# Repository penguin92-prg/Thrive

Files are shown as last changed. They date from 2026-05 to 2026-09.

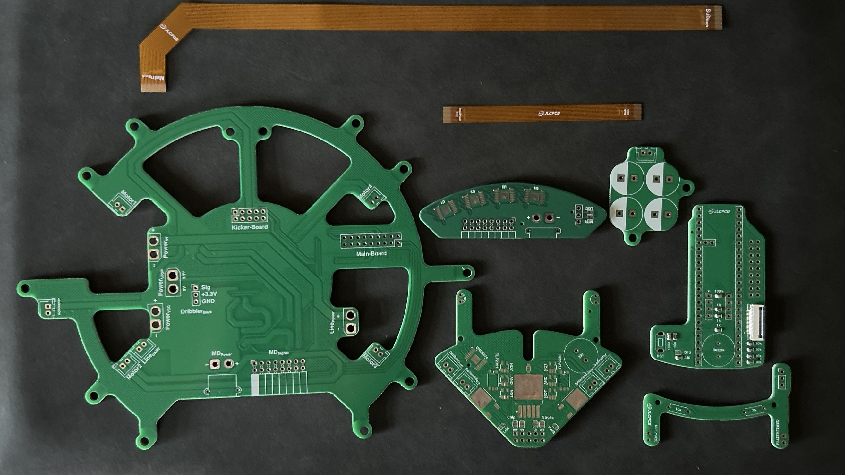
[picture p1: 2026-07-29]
Document/picture_substrate/Order-260707-1.jpg

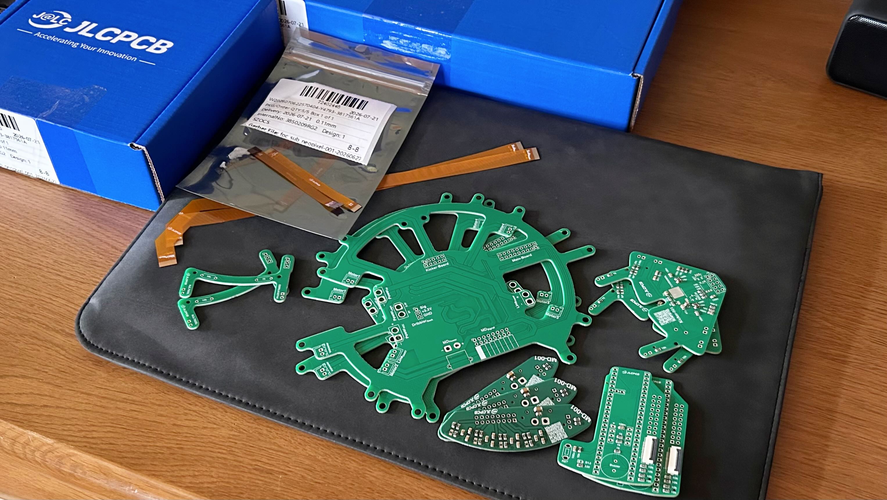
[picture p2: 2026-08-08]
Document/picture_substrate/Order-260707-2.jpg

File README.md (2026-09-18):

# Thrive 2026 Main-repo

このリポジトリは RCJ サッカー オープンリーグ に出場する、チーム Thrive のリポジトリです。

### Follow us!
様々な情報を公開していこうと考えています！ぜひのぞいてみてください！
- X (Twitter) | [@RCJ_thrive](https://x.com/RCJ_thrive)
- YouTube | [@RCJ_thrive](https://youtube.com/@rcj_thrive)
- Team Web Page | [Thrive Blog](https://note.com/rcj_thrive)

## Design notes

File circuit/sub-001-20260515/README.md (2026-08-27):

# サブ基板 001

サブ基板 ver.001のREADME

## 設計者
- @penguin92-prg
- @ryo-robot14

## ピンアサイン

## 使用上の注意

## 使用部品

|No.|Ref.|Name|QTY|Assembled By|Note|URL|
|---|---|---|---|---|---|---|
|001|U1,3,6,8,10|Grove|5|OWN|UnitV用（配線を介すること）|[秋月電子](https://akizukidenshi.com/catalog/g/g131074/)|
|002|U16,17|ESP32C3|2|OWN||[秋月電子](https://akizukidenshi.com/catalog/g/g117454/)<br>[秋月電子](https://akizukidenshi.com/catalog/g/g105779/)|
|003|D1,2,5~10|OSI5FU3A11C|8|OWN|IR-LED|[秋月電子](https://akizukidenshi.com/catalog/g/g104313/)|
|004|R5,6,17,18,27,28,39,40|Resister 47Ω|8|JLCPCB|IRLED用|[JLCPCB](https://jlcpcb.com/partdetail/18402-0805W8F470JT5E/C17714)|
|005|U4,5,12,13,18,19,22,23|NE555DR|8|JLCPCB|タイマーIC|[JLCPCB](https://jlcpcb.com/partdetail/TexasInstruments-NE555DR/C7593)|
|006|C2,3,8,9,14,15,21,22,27,28,33,34,37,38,43,44|Capacitor 10nF|16|JLCPCB|タイマーIC用|[JLCPCB](https://jlcpcb.com/partdetail/2062-CL21B103KBANNNC/C1710)|
|007|C4,5,17,18,29,30,39,40|Capacitor 1nF|8|JLCPCB|タイマーIC用|[JLCPCB](https://jlcpcb.com/partdetail/47657-CL21B102KBCNNNC/C46653)|
|008|C10,11,24,25,35,36,45,46|Capacitor 10uF|8|JLCPCB|タイマーIC用|[JLCPCB](https://jlcpcb.com/partdetail/439567-GRM21BR61H106KE43L/C440198)|
|009|R1,2,11,12,23,24,33,34|Resister 18kΩ|8|JLCPCB|タイマーIC用|[JLCPCB](https://jlcpcb.com/partdetail/18194-0805W8F1802T5E/C17506)|
|010|R3,4,13,14,25,26,37,38|Resister 1.5kΩ|8|JLCPCB|タイマーIC用|[JLCPCB](https://jlcpcb.com/partdetail/4717-0805W8F1501T5E/C4310)|
|011|R7,8,19,20,29,30,41,42|Resister 100Ω|8|JLCPCB|タイマーIC用|[JLCPCB](https://jlcpcb.com/partdetail/18096-0805W8F1000T5E/C17408)|
|012|R9,10,21,22,31,32,43,44|Resister 1kΩ|8|JLCPCB|タイマーIC用|[JLCPCB](https://jlcpcb.com/partdetail/18201-0805W8F1001T5E/C17513)|
|013|Q1~8|BSS138|8|OWN|NchMOSFET|[秋月電子](https://akizukidenshi.com/catalog/g/g104232/)|
|014|U20,21,24,25|tssp58038|4|OWN|IR Sensor|[秋月電子](https://akizukidenshi.com/catalog/g/g129594/)|
|015|C41/C42/C47/C48|Capacitor 0.33uF|4|JLCPCB|tssp58038用|[JLCPCB](https://jlcpcb.com/partdetail/2092-0805B334K500NT/C1740)|
|016|R35/R36/R45/R46|Resister 39kΩ|4|JLCPCB|tssp58038用|[JLCPCB](https://jlcpcb.com/partdetail/26569-0805W8F3902T5E/C25826)|
|017|U2,7,9,11,14,15|LM1117GS-3.3|6|OWN|3.3V生成3端子レギュレータ|[秋月電子](https://akizukidenshi.com/catalog/g/g116989/)|
|018|C1,6,7,12,13,16,19,20,23,26,31,32|Capacitor 10uF|12|JLCPCB|3端子レギュレータ用|[JLCPCB](https://jlcpcb.com/partdetail/439567-GRM21BR61H106KE43L/C440198)|
|019|D3|OSR50603C1E|1|OWN|5V給電確認用赤色LED|[秋月電子](https://akizukidenshi.com/catalog/g/g108274/)|
|020|D4|OSG50603C1E|1|ONW|3.3V給電確認用緑色LED|[秋月電子](https://akizukidenshi.com/catalog/g/g108275/)|
|021|R15,16|Resister 330Ω|2|JLCPCB|LED用抵抗器|[JLCPCB](https://jlcpcb.com/partdetail/18318-0805W8F3300T5E/C17630)|
|022|U26~29|HC-SR04|4|OWN|USS|[秋月電子](https://akizukidenshi.com/catalog/g/g111009/)|
|023|R47,48|Resister 10kΩ|2|JLCPCB|トグルスイッチプルアップ用抵抗器|[JLCPCB](https://jlcpcb.com/partdetail/18102-0805W8F1002T5E/C17414)|
|024|J1|AFC01_S12FCA00|1|JLCPCB|ネオピクセル基板へのFPCコネクタ|[JLCPCB](https://jlcpcb.com/partdetail/JUSHUO-AFC01_S12FCA00/C262661)|
|025|J2|ピンソケット 01x02|1|OWN|電源基板へのピンソケット|[秋月電子](https://akizukidenshi.com/catalog/g/g105779/)|
|026|J3|XT30U-M|1|OWN|電源基板へのXT30コネクタ|[秋月電子](https://akizukidenshi.com/catalog/g/g117951/)|
|027|J4|AFC01_S18FCA00|1|JLCPCB|メイン基板へのFPCコネクタ|[JLCPCB](https://jlcpcb.com/partdetail/JUSHUO-AFC01_S18FCA00/C262666)|

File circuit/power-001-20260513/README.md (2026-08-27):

# [基板名] [バージョン番号]

[基板名] ver.[バージョン番号]のREADME

## 設計者
- @penguin92-prg
- @ryo-robot14

## ピンアサイン

## 使用上の注意

## 使用部品

|No.|Ref.|Name|QTY|Assembled By|Note|URL|
|---|---|---|---|---|---|---|
|001|J1|Vin|1|OWN|not connected|--|
|002|J2,3,4,5|+5V_Line / Power / Logic / Sub_Power|4|OWN|XT30PW-M|[秋月電子](https://akizukidenshi.com/catalog/g/g117949/)|
|001|J6|Sub_Signal|1|OWN|ピンヘッダ 01x02|[秋月電子](https://akizukidenshi.com/catalog/g/g112986/)|
|001|J8|ESC|1|OWN|not connected|--|
|002|F1|Fuse 10A|1|OWN|ヒューズホルダー・ヒューズ|[秋月電子](https://akizukidenshi.com/catalog/g/g110521/)<br>[秋月電子](https://akizukidenshi.com/catalog/g/g107132/)|
|003|SW4|DS-850K-S-ON-K|1|OWN|ロッカースイッチ|[秋月電子](https://akizukidenshi.com/catalog/g/g115740/)|
|004|U5|PIC12F683T-I/SN|1|OWN|電圧監視IC|[秋月電子](https://akizukidenshi.com/catalog/g/g102034/)|
|005|C12|Capacitor 100nF|1|JLCPCB|電圧監視IC用コンデンサ|[JLCPCB](https://jlcpcb.com/partdetail/YAGEO-CC0805KRX7R9BB104/C49678)|
|006|R14|Resister 30kΩ|1|JLCPCB|電圧監視IC用抵抗器|[JLCPCB](https://jlcpcb.com/partdetail/18309-0805W8F3002T5E/C17621)|
|007|R15|Resister 10kΩ|2|JLCPCB|電圧監視IC用抵抗器|[JLCPCB](https://jlcpcb.com/partdetail/18102-0805W8F1002T5E/C17414)
|008|U6|LM1117GS-3.3|1|OWN|電圧監視IC用3端子レギュレータ|[秋月電子](https://akizukidenshi.com/catalog/g/g116989/)|
|009|C5,13|Capacitor 10uF|2|JLCPCB|3端子レギュレータ用コンデンサ|[JLCPCB](https://jlcpcb.com/partdetail/439567-GRM21BR61H106KE43L/C440198)|
|010|Q1|BSS138|1|OWN|NchMOSFET|[秋月電子](https://akizukidenshi.com/catalog/g/g104232)|
|011|Q2|TJ60S04M3L|1|OWN|PchパワーMOSFET|[秋月電子](https://akizukidenshi.com/catalog/g/g116297/)|
|012|R18|Resister 100Ω|1|JLCPCB||[JLCPCB](https://jlcpcb.com/partdetail/18096-0805W8F1000T5E/C17408)|
|013|R19,20|Resister 10kΩ|2|JLCPCB||[JLCPCB](https://jlcpcb.com/partdetail/18102-0805W8F1002T5E/C17414)|
|014|BZ1|PKM13EPYH4000-A0|1|OWN|電圧監視用ブザー|[秋月電子](https://akizukidenshi.com/catalog/g/g104118/)|
|015|R17|Resister 1.2kΩ|1|JLCPCB|ブザー用抵抗器|[JLCPCB](https://jlcpcb.com/partdetail/18067-0805W8F1201T5E/C17379)|
|016|C1|Capacitor 470uF|1|OWN||[秋月電子](https://akizukidenshi.com/catalog/g/g117883/)|
|017|U1,2|OKL-T/6-W12N-C|2|OWN|DCDC|[秋月電子](https://akizukidenshi.com/catalog/g/g106187/)|
|018|R4,5|Resister 20kΩ|2|JLCPCB|DCDC用抵抗器|[JLCPCB](https://jlcpcb.com/partdetail/4735-0805W8F2002T5E/C4328)|
|019|R6,7|Resister 10Ω|2|JLCPCB|DCDC用抵抗器|[JLCPCB](https://jlcpcb.com/partdetail/18103-0805W8F100JT5E/C17415)|
|020|R8,R10|Resister 1kΩ|2|JLCPCB|DCDC用抵抗器|[JLCPCB](https://jlcpcb.com/partdetail/18201-0805W8F1001T5E/C17513)|
|020|R9,11|Resister 330Ω|2|JLCPCB|DCDC用抵抗器|[JLCPCB](https://jlcpcb.com/partdetail/18318-0805W8F3300T5E/C17630)|
|020|R12,13|Resister 1.2kΩ|2|JLCPCB|DCDC用抵抗器|[JLCPCB](https://jlcpcb.com/partdetail/18067-0805W8F1201T5E/C17379)|
|020|C6,7|Capacitor 22uF|2|JLCPCB|DCDC用コンデンサ|[JLCPCB](https://jlcpcb.com/partdetail/46786-CL21A226MAQNNNE/C45783)|
|020|C10,11|Capacitor 10uF|2|JLCPCB|DCDC用コンデンサ|[JLCPCB](https://jlcpcb.com/partdetail/439567-GRM21BR61H106KE43L/C440198)|
|020|U3|AZ1084C-3.3|1|OWN|3端子レギュレータ|[秋月電子](https://akizukidenshi.com/catalog/g/g117598/)|
|020|C8|Capacitor 10uF|1|JLCPCB|3端子レギュレータ用コンデンサ|[JLCPCB](https://jlcpcb.com/partdetail/439567-GRM21BR61H106KE43L/C440198)|
|020|C9|Capacitor 22uF|1|JLCPCB|3端子レギュレータ用コンデンサ|[JLCPCB](https://jlcpcb.com/partdetail/46786-CL21A226MAQNNNE/C45783)|
|020|SW1,2|トグルスイッチ|1|OWN||[秋月電子](https://akizukidenshi.com/catalog/g/g102399/)|
|020|C2,3|Capacitor 100nF|2|JLCPCB|トグルスイッチ用コンデンサ|[JLCPCB](https://jlcpcb.com/partdetail/YAGEO-CC0805KRX7R9BB104/C49678)|

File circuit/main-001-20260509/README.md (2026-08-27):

# Main 001

メイン基板 ver.001のREADME

## 設計者
- @ryo-robot14
- @penguin92-prg

## ピンアサイン

## 使用上の注意

## 使用部品

|No.|Ref.|Name|QTY|Assembled By|Note|URL|
|---|---|---|---|---|---|---|
|001|U1|Teensy4.1|1|OWN|側面の24ピン×2に加えてSDスロット側の5ピンのうち2ピンもつける必要アリ|[PJRC](https://www.pjrc.com/store/teensy41.html)<br>[秋月電子](https://akizukidenshi.com/catalog/g/g105779/)|
|002|U2|BNO055 Module|1|OWN||[秋月電子](https://akizukidenshi.com/catalog/g/g116996/)|
|003|J1|ピンヘッダ 02x09|1|OWN|基板カッターで02x09に加工する必要がある|[秋月電子](https://akizukidenshi.com/catalog/g/g100082/)|
|004|Q1/Q2|BSS138|2|OWN|UART通信のレベル変換用|[秋月電子](https://akizukidenshi.com/catalog/g/g104232)|
|005|J2|AFC01-S18FCA-00|1|JLCPCB|サブ基板へのFPCコネクタ|[JLCPCB](https://jlcpcb.com/partdetail/JUSHUO-AFC01_S18FCA00/C262666)|
|006|BZ1|PKM13EPYH4000-A0|1|OWN|ブザー|[秋月電子](https://akizukidenshi.com/catalog/g/g104118/)|
|007|SW1|TVBP06-B043CW-B|1|OWN|白タクトスイッチ|[秋月電子](https://akizukidenshi.com/catalog/g/g108074/)|
|008|D1|OSWT1608C1A|1|OWN|青色LED(SMD)|[秋月電子](https://akizukidenshi.com/catalog/g/g103986/)|

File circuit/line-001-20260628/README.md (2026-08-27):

# ラインセンサ基板 001

ラインセンサ基板 ver.001のREADME

## 設計者
- @penguin92-prg
- @ryo-robot14

## ピンアサイン

## 使用上の注意

## 使用部品

|No.|Ref.|Name|QTY|Assembled By|Note|URL|
|---|---|---|---|---|---|---|
|001|D1~40|OSR5JA3Z74A|40|OWN|赤色LED|[秋月電子](https://akizukidenshi.com/catalog/g/g111577/)|
|002|R41~72,77~80|Resister 10kΩ|34|JLCPCB|LED用75Ω|[JLCPCB](https://jlcpcb.com/partdetail/21350-0805W8F750JT5E_SMTonly/C20638)|
|003|Q1~40|NJL7502L|40|OWN|フォトトランジスタ|[秋月電子](https://akizukidenshi.com/catalog/g/g102325/)|
|004|R1~32,38,40|Resister 10kΩ|34|JLCPCB|プルダウン用100kΩ|[JLCPCB](https://jlcpcb.com/partdetail/18102-0805W8F1002T5E/C17414)|
|005|U1~16,19,20|LM339DR|20|JLCPCB|コンパレータ|[JLCPCB](https://jlcpcb.com/partdetail/TexasInstruments-LM393DR/C67470)|
|006|C1~16,23,24|Capacitor 100nF|20|JLCPCB|コンパレータ用バイパスコンデンサ|[JLCPCB](https://jlcpcb.com/partdetail/YAGEO-CC0805KRX7R9BB104/C49678)|
|007|C21,22,26,27|Capacitor 10uF|4|JLCPCB|PWM平滑化用コンデンサ|[JLCPCB](https://jlcpcb.com/partdetail/439567-GRM21BR61H106KE43L/C440198)|
|008|R83,84,87,88|Resister 1kΩ|4|JLCPCB|PWM平滑化用抵抗器|[JLCPCB](https://jlcpcb.com/partdetail/18201-0805W8F1001T5E/C17513)|
|009|U17|ATMega2560-16A|1|OWN||[秋月電子](https://akizukidenshi.com/catalog/g/g116567/)|
|010|C28|Capacitor 100nF|1|JLCPCB|ATMegaARFF用コンデンサ|[JLCPCB](https://jlcpcb.com/partdetail/YAGEO-CC0805KRX7R9BB104/C49678)|
|011|SW1|TVBP06-B043C|1|OWN|ATMegaRST用白色タクトスイッチ|[秋月電子](https://akizukidenshi.com/catalog/g/g108074/)|
|012|C18|Capacitor 100nF|1|JLCPCB|ATMegaRST用コンデンサ|[JLCPCB](https://jlcpcb.com/partdetail/YAGEO-CC0805KRX7R9BB104/C49678)|
|013|R81|Resister 10kΩ|1|JLCPCB|ATMegaRST用抵抗器|[JLCPCB](https://jlcpcb.com/partdetail/18102-0805W8F1002T5E/C17414)|
|014|C20|Capacitor 100uF|1|JLCPCB|ATMega用バルクコンデンサ|[JLCPCB](https://jlcpcb.com/partdetail/15681-CL31A107MQHNNNE/C15008)|
|015|C34~38|Capacitor 100nF|5|JLCPCB|ATMega用バイパスコンデンサ|[JLCPCB](https://jlcpcb.com/partdetail/YAGEO-CC0805KRX7R9BB104/C49678)|
|016|SW2|SS12D01G4|1|OWN|5V切り替え用スライドスイッチ|[秋月電子](https://akizukidenshi.com/catalog/g/g112723/)|
|017|J3|コネクタハウジング 02x03|1|OWN|ICSP用ハウジング（配線を介すること）|[秋月電子](https://akizukidenshi.com/catalog/g/g112435/)|
|018|D41|OSG50603C1E|1|OWN|信号緑色LED|[秋月電子](https://akizukidenshi.com/catalog/g/g108275/)|
|019|D42|OSWT1608C1A|1|OWN|信号青色LED|[秋月電子](https://akizukidenshi.com/catalog/g/g103986/)|
|020|R85,86|Resister 330Ω|2|JLCPCB|LED用抵抗器|[JLCPCB](https://jlcpcb.com/partdetail/18318-0805W8F3300T5E/C17630)|
|021|U18|CH340G|1|OWN|USB-UART変換IC|[秋月電子](https://akizukidenshi.com/catalog/g/g113544/)|
|022|C31,32,33|Capacitor 100nF|3|JLCPCB|CH340G用コンデンサ|[JLCPCB](https://jlcpcb.com/partdetail/YAGEO-CC0805KRX7R9BB104/C49678)|
|023|R93|Resister 4.7kΩ|1|JLCPCB|CH340G用抵抗器|[JLCPCB](https://jlcpcb.com/partdetail/18361-0805W8F4701T5E/C17673)|
|024|Y1|Crystal 16MHz|1|OWN|クリスタル|[秋月電子](https://akizukidenshi.com/catalog/g/g108671/)|
|025|C17,19|Capacitor 22pF|2|JLCPCB|クリスタル用コンデンサ|[JLCPCB](https://jlcpcb.com/partdetail/2005-CL10C220JB8NNNC/C1653)|
|026|R82|Resister 1MΩ||JLCPCB|クリスタル用抵抗器|[JLCPCB](https://jlcpcb.com/partdetail/18202-0805W8F1004T5E/C17514)|
|027|Y2|Crystal 12MHz|1|OWN|クリスタル|[秋月電子](https://akizukidenshi.com/catalog/g/g108669/)|
|028|C29,30|Capacitor 22pF|2|JLCPCB|クリスタル用コンデンサ|[JLCPCB](https://jlcpcb.com/partdetail/2005-CL10C220JB8NNNC/C1653)|
|029|R89|Resister 1MΩ|1|JLCPCB|クリスタル用抵抗器|[JLCPCB](https://jlcpcb.com/partdetail/18202-0805W8F1004T5E/C17514)|
|030|P1|USB Type-C|1|OWN|1|[秋月電子](https://akizukidenshi.com/catalog/g/g114356/)|
|031|R90,91|Resister 5.1kΩ|2|JLCPCB|USB用抵抗器|[JLCPCB](https://jlcpcb.com/partdetail/28584-0805W8F5101T5E/C27834)|
|032|D43|CH213K|1|OWN|USB用理想ダイオード|[秋月電子](https://akizukidenshi.com/catalog/g/g129462/)|
|033|D44|OSR50603C1E|1|OWN|VBUS確認用LED|[秋月電子](https://akizukidenshi.com/catalog/g/g108274/)|
|034|R92|Resister 330Ω|1|JLCPCB|VBUS確認用抵抗器|[JLCPCB](https://jlcpcb.com/partdetail/18318-0805W8F3300T5E/C17630)|
|035|J1|XT30U-M|1|OWN|供給基板との接続|[秋月電子](https://akizukidenshi.com/catalog/g/g117951/)|
|036|J2|---|-|---|2pin配線を直接実装すること|---|

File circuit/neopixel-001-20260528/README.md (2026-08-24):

# ネオピクセル基板 001

ネオピクセル基板 ver.001のREADME

## 設計者
- @penguin92-prg
- @ryo-robot14

## ピンアサイン

## 使用上の注意

## 使用部品

|No.|Ref.|Name|QTY|Assembled By|Note|URL|
|---|---|---|---|---|---|---|
|001|D1~D16|WS2812B|16|OWN|WS2812B(NeoPixel)|[秋月電子](https://akizukidenshi.com/catalog/g/g107915/)|
|002|C1~C16|Capacitor 100nF|16|JLCPCB|WS2812B用バイパスコンデンサ|[JLCPCB](https://jlcpcb.com/partdetail/YAGEO-CC0805KRX7R9BB104/C49678)|
|003|R9,10|Resister 500Ω|2|JLCPCB|WS2812B用|[JLCPCB](https://jlcpcb.com/partdetail/VikingTech-ARG05FTC5000/C2828857)|
|004|SW1,2,4|ST12-401FCG|3|OWN|タクトスイッチ・赤色LED内蔵|[秋月電子](https://akizukidenshi.com/catalog/g/g102010/)|
|005|C17,18,19|Capacitor 100nF|3|JLCPCB|スイッチ用|[JLCPCB](https://jlcpcb.com/partdetail/YAGEO-CC0805KRX7R9BB104/C49678)|
|006|R3,5,7|Resister 10kΩ|3|JLCPCB|スイッチ用|[JLCPCB](https://jlcpcb.com/partdetail/18102-0805W8F1002T5E/C17414)|
|007|R4,6,8|Resister 330Ω|3|JLCPCB|スイッチ用|[JLCPCB](https://jlcpcb.com/partdetail/18318-0805W8F3300T5E/C17630)|
|008|Q1~3|NchMOSFET|3|OWN|スイッチ用・BSS138|[秋月電子](https://akizukidenshi.com/catalog/g/g104232/)|
|009|U3~5|NOT回路 インバータ|3|OWN|スイッチ用・74AHC1G04W5|[秋月電子](https://akizukidenshi.com/catalog/g/g117602/)|
|010|U1|SSD1306|1|OWN|ディスプレイ・端を切る必要あり|[秋月電子](https://akizukidenshi.com/catalog/g/g112031/)|
|011|R1,2|Resister 1kΩ|2|JLCPCB|SSD1306用プルアップ抵抗|[JLCPCB](https://jlcpcb.com/partdetail/18201-0805W8F1001T5E/C17513)|
|012|J1|AFC01_S12FCA00|1|JLCPCB|サブ基板へのFPCコネクタ|[JLCPCB](https://jlcpcb.com/partdetail/JUSHUO-AFC01_S12FCA00/C262661)|
|013|J2|B2B-XH-A|1|OWN|キッカー基板からの48Vライン|[秋月電子](https://akizukidenshi.com/catalog/g/g112247/)|
|014|J3|B2B-XH-A|1|OWN|コンデンサ基板への48Vライン|[秋月電子](https://akizukidenshi.com/catalog/g/g112247/)|
|015|U2|Aexit Voltmeter|1|OWN|50Vまで測れる電圧計|[Amazon](https://www.amazon.co.jp/dp/B07D5W5FMP?ref=ppx_yo2ov_dt_b_fed_asin_title)|
|016|P1,3,5,7,9,11|USB Type-C Horizontal|6|OWN||[秋月電子](https://akizukidenshi.com/catalog/g/g114356)|
|017|P2,4,6,8,10,12|USB Type-C Vertical|6|JLCPCB||[JLCPCB](https://jlcpcb.com/partdetail/HanboElectronic-MC_118LDH65/C6332304)|

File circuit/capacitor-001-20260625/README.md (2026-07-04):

# Capacitor 001

コンデンサ基板 ver.001のREADME

## 設計者
- @ryo-robot14
- @penguin92-prg

## 使用上の注意
- 面付け済み（マウスバイト）なため、基板を切り離した後は側面をヤスリがけする

## 使用部品

|No.|Ref.|Name|QTY|Assembled By|Note|URL|
|---|---|---|---|---|---|---|
|001|C1/C2/C3/C4|ルビコンPX 1000μF 50V|4|OWN|昇圧済み電源の蓄電用|[秋月電子](https://akizukidenshi.com/catalog/g/g113081/)|
|002|J1|B2B-XH-A|1|OWN|サブ基板との接続用|[秋月電子](https://akizukidenshi.com/catalog/g/g112247/)|

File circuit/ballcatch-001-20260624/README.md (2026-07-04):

# BallCatch 001

ボール補足基板 ver.001のREADME

## 設計者
- @ryo-robot14
- @penguin92-prg

## 使用上の注意

## 使用部品

|No.|Ref.|Name|QTY|Assembled By|Note|URL|
|---|---|---|---|---|---|---|
|001|Q1|NJL7502L|1|OWN|ボール補足用フォトトランジスタ|[秋月電子](https://akizukidenshi.com/catalog/g/g102325/)|
|002|D1|OSR5JA3Z74A|1|OWN|ボール補足用LED|[秋月電子](https://akizukidenshi.com/catalog/g/g111577/)|
|003|J1|ピンヘッダ 01x03|1|OWN|キッカー基板への接続用|[秋月電子](https://akizukidenshi.com/catalog/g/g100167/)|
|004|R1|カーボン抵抗 1/4W 75Ω|1|OWN|LED用抵抗|[秋月電子](https://akizukidenshi.com/catalog/g/g125750/)|
|005|R2|カーボン抵抗 1/4W 10KΩ|1|OWN|プルダウン用抵抗|[秋月電子](https://akizukidenshi.com/catalog/g/g125103/)|

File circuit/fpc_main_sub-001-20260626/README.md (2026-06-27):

# FPC-Main-Sub 001

FPC-Main-Sub ver.001のREADME

## 設計者
- @penguin92-prg

## 使用上の注意

## 使用部品

|No.|Name|QTY|Assembled By|Note|URL|
|---|---|---|---|---|---|
|001|AFC01-S18FCA-00|0|(no assembly)||[JLCPCB](https://jlcpcb.com/partdetail/JUSHUO-AFC01_S18FCA00/C262666)|

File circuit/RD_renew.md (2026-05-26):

# PCB要件定義

### `寺田`
- MD基板
- キッカー基板
- ラインセンサ基板
- 電源基板

### `貝尻`
- メイン基板
- サブ基板
- (中継基板)

### `基板`
- ボール保持検知基板
- NeoPixel基板
- (ディスプレイ基板)
- (スイッチ用基板)

## `メイン基板`
### 使用部品と機能
- [Teensy4.1](https://www.pjrc.com/store/teensy41.html)
  - MD基板へのモーター操作信号の出力
  - ロボット同士の相互位置取得用IRセンサの信号取得・処理
  - ドリブラー操作信号の出力
  - キッカー基板との通信(3.3V)
  - トグル/タクトスイッチ類の信号処理
  - ボール保持検知基板との通信(3.3V)
  - スイッチ基板との通信(3.3V)
  - BNO055モジュールとのI2C通信
  - M5UnitV (5x) とのUART通信
  - ATMEGA2560 on ラインセンサ基板 とのUART通信
  - ESP32C3 | 1 on サブ基板 とのUART通信(3.3V)
  - ESP32C3 | 2 on サブ基板 とのUART通信(3.3V)
- [BNO055 9軸センサモジュール](https://akizukidenshi.com/catalog/g/g116996/)
  - 基板に直付け(ピンソケット/ヘッダ)
  - I2Cは1KΩでPULLUPしておく
- [圧電ブザー | PKM13EPYH4000-A0](https://akizukidenshi.com/catalog/g/g104118/)
- [PinSocket](https://akizukidenshi.com/catalog/g/g105779/)
  - メイン基板への電源供給線
    - GND/5V/3.3V
  - ドリブラーとの通信線
- [BSS138](https://akizukidenshi.com/catalog/g/g104232)
  - ラインセンサとの通信のレベル変換(3.3v/5V)
- [XH 03B F](https://akizukidenshi.com/catalog/g/g112248/)
  - ※ ピンソケットが高さ的に合わない場合
  - メイン基板への電源供給線
- FPC
  - ラインセンサ基板との通信線
  - サブ基板との通信
  - スイッチ基板との通信

## `MD基板`
### 使用部品と機能
- [DRV8874](https://www.digikey.jp/ja/products/detail/texas-instruments/DRV8874PWPR/11502339)
  - モータードライバ素子
  - maxonモーターはLAP駆動で操作予定
  - 5コ搭載予定
    - 4コは駆動モータ
    - 1コは前ドリブラー (IG22/秋月モーター 1:1)
- [PinSocket | 1](https://akizukidenshi.com/catalog/g/g105779/)
  - 中継基板に接続
  - モーターが直接接続するのはMD基板ではなく中継基板
- [PinSocket | 2](https://akizukidenshi.com/catalog/g/g105779/)
  - 中継基板に接続
  - モーター駆動用信号をマイコンから伝達
- [XT30 B M](https://akizukidenshi.com/catalog/g/g117951/)
  - MD基板への電源供給線
  - 中継基板と接続

## `キッカー基板`
### 使用部品と機能
- [XL6009e1](https://www.aitendo.com/product/10307)
  - 11.1VDCを40VDC程度まで昇圧し両キッカー用高電圧電源の生成
- [PinSocket](https://akizukidenshi.com/catalog/g/g105779/)
  - 中継基板に接続
  - キッカー基板への電源供給線
- [XH 02B F](https://akizukidenshi.com/catalog/g/g112247/)
  - ソレノイドとの接続
- [C 2200μF 50V ルビコンPX](https://akizukidenshi.com/catalog/g/g113243/)
  - キッカー用電源の蓄電
  - 同時に逆起電圧の緩和

## `ラインセンサ基板`
### 使用部品と機能
- [ATMEGA2560-16AUR](https://akizukidenshi.com/catalog/g/g116567/)
  - 照度センサ素子の信号取得・処理
  - コンパレータの比較電圧の出力（PWMを平滑化）
  - メインマイコン(Teensy4.1)とのUART通信
  - (LEDの明るさの調整?)
- [NJL7502L](https://akizukidenshi.com/catalog/g/g102325/)
  - 反射光の照度計測
  - THT
  - 照度センサは38コ
    - 円形に32コ（個別監視）
    - 左右のみ一回り大きい円形で3コずつ（並列でまとめて監視）
- [OSR5JA3Z74A](https://akizukidenshi.com/catalog/g/g111577/)
  - 地面を照らして反射光を生成
- [LM393DR2G](https://www.digikey.jp/ja/products/detail/onsemi/LM393DR2G/918527)
  - ATMEGAの平滑化された比較電圧と照度センサの値を比較
- [圧電ブザー | PKM13EPYH4000-A0](https://akizukidenshi.com/catalog/g/g104118/)

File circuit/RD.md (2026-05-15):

# PCB要件定義

- メイン基板
- サブ基板
- MD基板
- キッカー基板
- ラインセンサ基板
- 電源基板
- ボール保持検知基板
- (中継基板)
- (スイッチ用基板)

## `メイン基板`
### 使用部品と機能
- [Teensy4.1](https://www.pjrc.com/store/teensy41.html)
  - MD基板へのモーター操作信号の出力
  - ロボット同士の相互位置取得用IRセンサの信号取得・処理
  - ドリブラー操作信号の出力
  - キッカー基板との通信(3.3V)
  - トグル/タクトスイッチ類の信号処理
  - ボール保持検知基板との通信(3.3V)
  - スイッチ基板との通信(3.3V)
  - BNO055モジュールとのI2C通信
  - M5UnitV (5x) とのUART通信
  - ATMEGA2560 on ラインセンサ基板 とのUART通信
  - ESP32C3 | 1 on サブ基板 とのUART通信(3.3V)
  - ESP32C3 | 2 on サブ基板 とのUART通信(3.3V)
- [BNO055 9軸センサモジュール](https://akizukidenshi.com/catalog/g/g116996/)
  - 基板に直付け(ピンソケット/ヘッダ)
  - I2Cは1KΩでPULLUPしておく
- [圧電ブザー | PKM13EPYH4000-A0](https://akizukidenshi.com/catalog/g/g104118/)
- ピンソケット
  - メイン基板への電源供給線
    - GND/5V/3.3V
  - ドリブラーとの通信線
- [BSS138](https://akizukidenshi.com/catalog/g/g104232)
  - ラインセンサとの通信のレベル変換(3.3v/5V)
- [XH 03B F](https://akizukidenshi.com/catalog/g/g112248/)
  - ※ ピンソケットが高さ的に合わない場合
  - メイン基板への電源供給線
- FPC
  - ラインセンサ基板との通信線
  - サブ基板との通信
  - スイッチ基板との通信

## `サブ基板`
### 使用部品と機能
- [ESP32C3 | 1](https://akizukidenshi.com/catalog/g/g117454/)
  - 超音波センサの信号取得・処理
  - NeoPixel操作信号の出力
  - ディスプレイとのI2C通信
  - 2機体間のBluetooth通信
- [ESP32C3 | 2](https://akizukidenshi.com/catalog/g/g117454/)
  - ?
- [SSD1306使用 ディスプレイモジュール](https://akizukidenshi.com/catalog/g/g112031/)
  - 機体UIとして使用
- [HC-SR04](https://akizukidenshi.com/catalog/g/g111009/)
  - コート壁との距離を測定
- FPC
  - メイン基板との電源/通信線

## `MD基板`
### 使用部品と機能
- [DRV8874](https://www.digikey.jp/ja/products/detail/texas-instruments/DRV8874PWPR/11502339)
  - モータードライバ素子
  - maxonモーターはLAP駆動で操作予定
- [XH 02B F](https://akizukidenshi.com/catalog/g/g112247/)
  - maxonモーター用配線
- [XT30 B M](https://akizukidenshi.com/catalog/g/g117951/)
  - MD基板への電源供給線

## `キッカー基板`
### 使用部品と機能
- [XL6009 module](https://www.aitendo.com/product/10257)
  - 11.1VDCを40VDC程度まで昇圧し両キッカー用高電圧電源の生成
- [XH 02B F](https://akizukidenshi.com/catalog/g/g112247/)
  - キッカー基板への電源供給線
  - ソレノイド用配線
- [C 2200μF 50V ルビコンPX](https://akizukidenshi.com/catalog/g/g113243/)
  - キッカー用電源の蓄電
  - 同時に逆起電圧の緩和

## `ラインセンサ基板`
### 使用部品と機能
- [ATMEGA2560-16AUR](https://akizukidenshi.com/catalog/g/g116567/)
  - 照度センサ素子の信号取得・処理
  - コンパレータの比較電圧の出力（PWMを平滑化）
  - メインマイコン(Teensy4.1)とのUART通信
  - (LEDの明るさの調整?)
- [NJL7502L](https://akizukidenshi.com/catalog/g/g102325/)
  - 反射光の照度計測
- [OSWT3166B](https://akizukidenshi.com/catalog/g/g100992/)
  - 地面を照らして反射光を生成
- [LM393DR2G](https://www.digikey.jp/ja/products/detail/onsemi/LM393DR2G/918527)
  - ATMEGAの平滑化された比較電圧と照度センサの値を比較

## `電源基板`
### 使用部品と機能
- [OKL-T/6-W12N-C](https://akizukidenshi.com/catalog/g/g106187/)
  - 電源電圧からロジック電圧(5V/3.3V)を生成
- [XH 02B F](https://akizukidenshi.com/catalog/g/g112247/)
  - キッカー基板への電源供給線
- [XH 03B F](https://akizukidenshi.com/catalog/g/g112248/)
  - メイン基板への電源供給線
- [XT30 B M](https://akizukidenshi.com/catalog/g/g117951/)
  - ラインセンサ基板への電源供給線
  - MD基板への電源供給線
- LiPoのコネクタ(VHコネクタ?)
  - 電源基板への電源供給線

## `ボール保持検知基板`
### 使用部品と機能
- [NJL7502L](https://akizukidenshi.com/catalog/g/g102325/)
  - ボールによる反射光の照度計測
- [OSWT3166B](https://akizukidenshi.com/catalog/g/g100992/)
  - ボールを照らして反射光を生成

## `(中継基板)`

## `(スイッチ用基板)`

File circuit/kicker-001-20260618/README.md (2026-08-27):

# Kicker 001

キッカー基板 ver.001のREADME

## 設計者
- @penguin92-prg
- @ryo-robot14

## 使用上の注意

- ソレノイドが2種類あるため注意
  - 通常キック用ソレノイド「Stroke」
  - チップキック用ソレノイド「Chip」
- ワンショット回路組み込み済み
  - 1000ms程度で連続通電を回路的に遮断する
  - 過信しすぎず、まずはプログラム側での制御を！
  - ワンショット回路を使用するかどうかは基板表面のジャンパで切り替え可能
    - 2コのソレノイドそれぞれに対してONとOFFの2種のジャンパがある
    - 設定したい方のジャンパをはんだ付けして導通させること

## 使用部品

|No.|Ref.|Name|QTY|Assembled By|Note|URL|
|---|---|---|---|---|---|---|
|001|U3|XL6009E1|1|OWN|昇圧素子|[Aitendo](https://www.aitendo.com/product/10307)|
|002|Q1|BSS138|1|OWN|昇圧素子への給電EN用NMOS|[秋月電子](https://akizukidenshi.com/catalog/g/g104232)|
|003|Q2|TJ15S06M3L|1|OWN|昇圧素子への給電EN用PMOS|[秋月電子](https://akizukidenshi.com/catalog/g/g117253/)|
|004|Q4/Q5|MTB010N06RJ3|2|OWN|ソレノイドスイッチング用NMOS|[秋月電子](https://akizukidenshi.com/catalog/g/g117074/)|
|005|U2/U9/U10|TLP2361|3|OWN|フォトカプラ|[秋月電子](https://akizukidenshi.com/catalog/g/g111004/)|
|006|U1/U4/U5/U7/U8|74AHC1G04W5|5|OWN|NOTゲート（インバータ）|[秋月電子](https://akizukidenshi.com/catalog/g/g117602/)|
|007|U11/U12|74AHC1G08W5|2|OWN|ANDゲート|[秋月電子](https://akizukidenshi.com/catalog/g/g117603/)|
|008|U6|DRV8874PWPR|1|OWN|ドリブラー制御用MD|[DigiKey](https://www.digikey.jp/ja/products/detail/texas-instruments/DRV8874PWPR/11502339)|
|009|Q3|NJL7502L|1|OWN|ボール補足用フォトトランジスタ|[秋月電子](https://akizukidenshi.com/catalog/g/g102325/)|
|010|D1|OSR5JA3Z74A|1|OWN|ボール補足用LED|[秋月電子](https://akizukidenshi.com/catalog/g/g111577/)|
|011|J4|ピンヘッダ 02x05|1|OWN|供給基板との接続|[秋月電子](https://akizukidenshi.com/catalog/g/g100167/)|
|012|J1/J2/J3/J6|B2B-XH-A|4|OWN|前ドリブラー/ソレノイド-Stroke/ソレノイド-Chip/コンデンサ基板|[秋月電子](https://akizukidenshi.com/catalog/g/g112247/)|
|013|D2|CUHS20F60|1|OWN|昇圧素子用ダイオード|[秋月電子](https://akizukidenshi.com/catalog/g/g116782/)|
|014|L1|SRC1317|1|OWN|昇圧素子用インダクタ|[秋月電子](https://akizukidenshi.com/catalog/g/g116276/)|
|015|D3|OSR50603C1E|1|OWN|VCC確認用赤色LED|[秋月電子](https://akizukidenshi.com/catalog/g/g108274/)|
|016|D4|OSG50603C1E|1|OWN|LGC確認用緑色LED|[秋月電子](https://akizukidenshi.com/catalog/g/g108275/)|

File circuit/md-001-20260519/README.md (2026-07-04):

# MD 001

MD基板 ver.001のREADME

## 設計者
- @penguin92-prg
- @ryo-robot14

## 使用上の注意

## 使用部品

|No.|Ref.|Name|QTY|Assembled By|Note|URL|
|---|---|---|---|---|---|---|
|001|U1/U2/U3/U4|DRV8874PWPR|4|OWN||[DigiKey](https://www.digikey.jp/ja/products/detail/texas-instruments/DRV8874PWPR/11502339)|
|002|J1|XT30PW-F 01x02|1|OWN|供給基板からの給電|[秋月電子](https://akizukidenshi.com/catalog/g/g117948/)|
|003|J2|ピンソケット 01x03|1|OWN|ボール補足基板との接続|[秋月電子](https://akizukidenshi.com/catalog/g/g105779/)|
|004|J3|ピンヘッダ L型 02×08|1|OWN|供給基板との接続<br>基板カッターで02x08に加工する必要がある|[秋月電子](https://akizukidenshi.com/catalog/g/g100082/)|
|005|D1|OSR50603C1E|1|OWN|VCC確認用赤色LED|[秋月電子](https://akizukidenshi.com/catalog/g/g108274/)|
|006|D2|OSG50603C1E|1|OWN|LGC確認用緑色LED|[秋月電子](https://akizukidenshi.com/catalog/g/g108275/)|

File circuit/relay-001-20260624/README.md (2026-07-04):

# Relay 001

供給基板 ver.001のREADME

## 設計者
- @ryo-robot14
- @penguin92-prg

## 使用上の注意

## 使用部品

|No.|Ref.|Name|QTY|Assembled By|Note|URL|
|---|---|---|---|---|---|---|
|001|J11/J12/J13/J14/J9/J15|B2B-XH-A|6|OWN|モーター1･2･3･4への出力/ラインセンサ基板との通信/電圧計|[秋月電子](https://akizukidenshi.com/catalog/g/g112247/)|
|002|J10|XT30PW-F 01x02|1|OWN|MD基板への給電|[秋月電子](https://akizukidenshi.com/catalog/g/g117948/)|
|003|J5/J6/J7/J8|XT30U-M 01x02|4|OWN|電源基板との接続1･2･3/ラインセンサ基板への給電|[秋月電子](https://akizukidenshi.com/catalog/g/g117951/)|
|004|J2|ピンソケット 02x05|1|OWN|キッカー基板との接続|[秋月電子](https://akizukidenshi.com/catalog/g/g100168/)|
|005|J4|ピンソケット 02x09|1|OWN|メイン基板との接続|[秋月電子](https://akizukidenshi.com/catalog/g/g100083/)|
|006|J3|ピンソケット L型 02×08|1|OWN|MD基板との接続<br>基板カッターで02x08に加工する必要がある|[秋月電子](https://akizukidenshi.com/catalog/g/g131515/)|
|007|J1|ピンヘッダ 01x03|1|OWN|後ろドリブラーへの出力|[秋月電子](https://akizukidenshi.com/catalog/g/g100167/)|

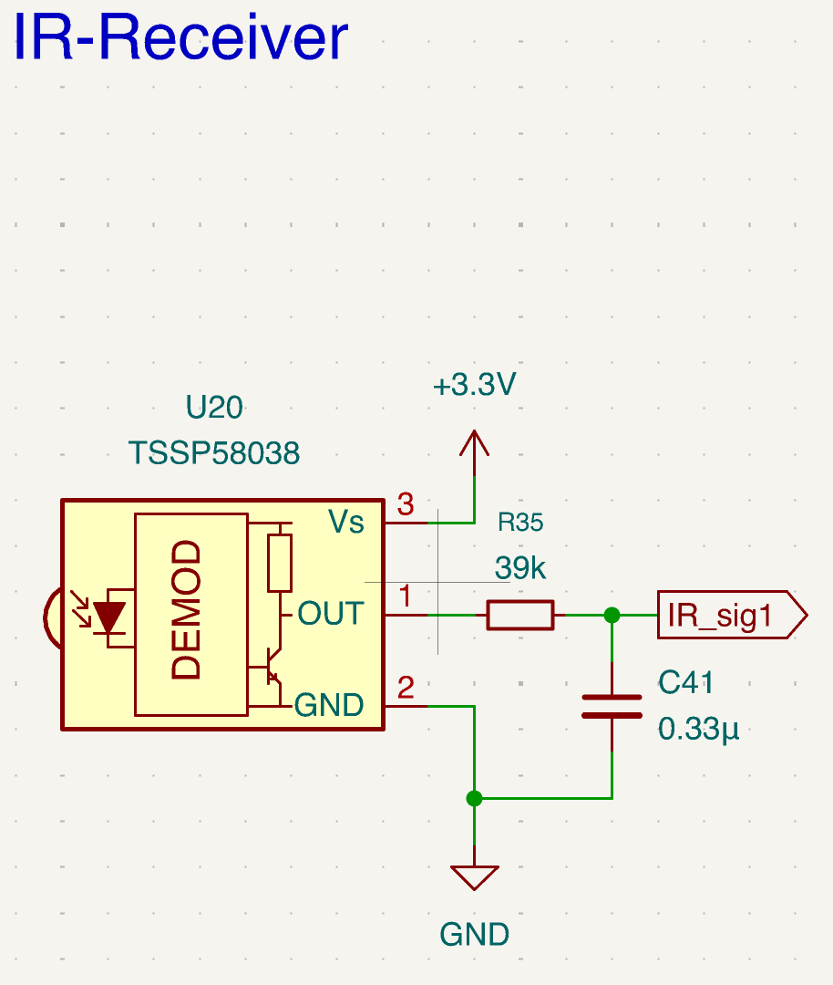
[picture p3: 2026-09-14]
circuit/sub-001-20260515/sub-schematic-ir-receiver.png

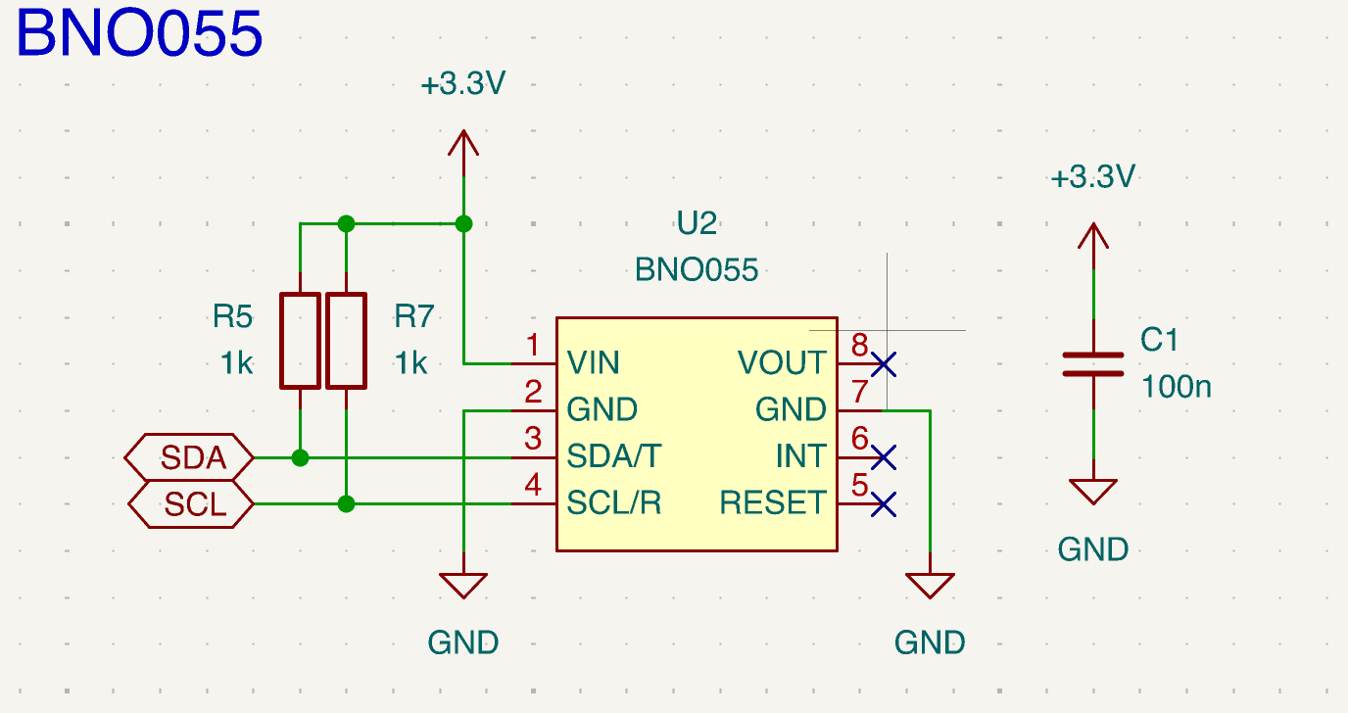
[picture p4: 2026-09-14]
circuit/main-001-20260509/main-schematic-bno055.png

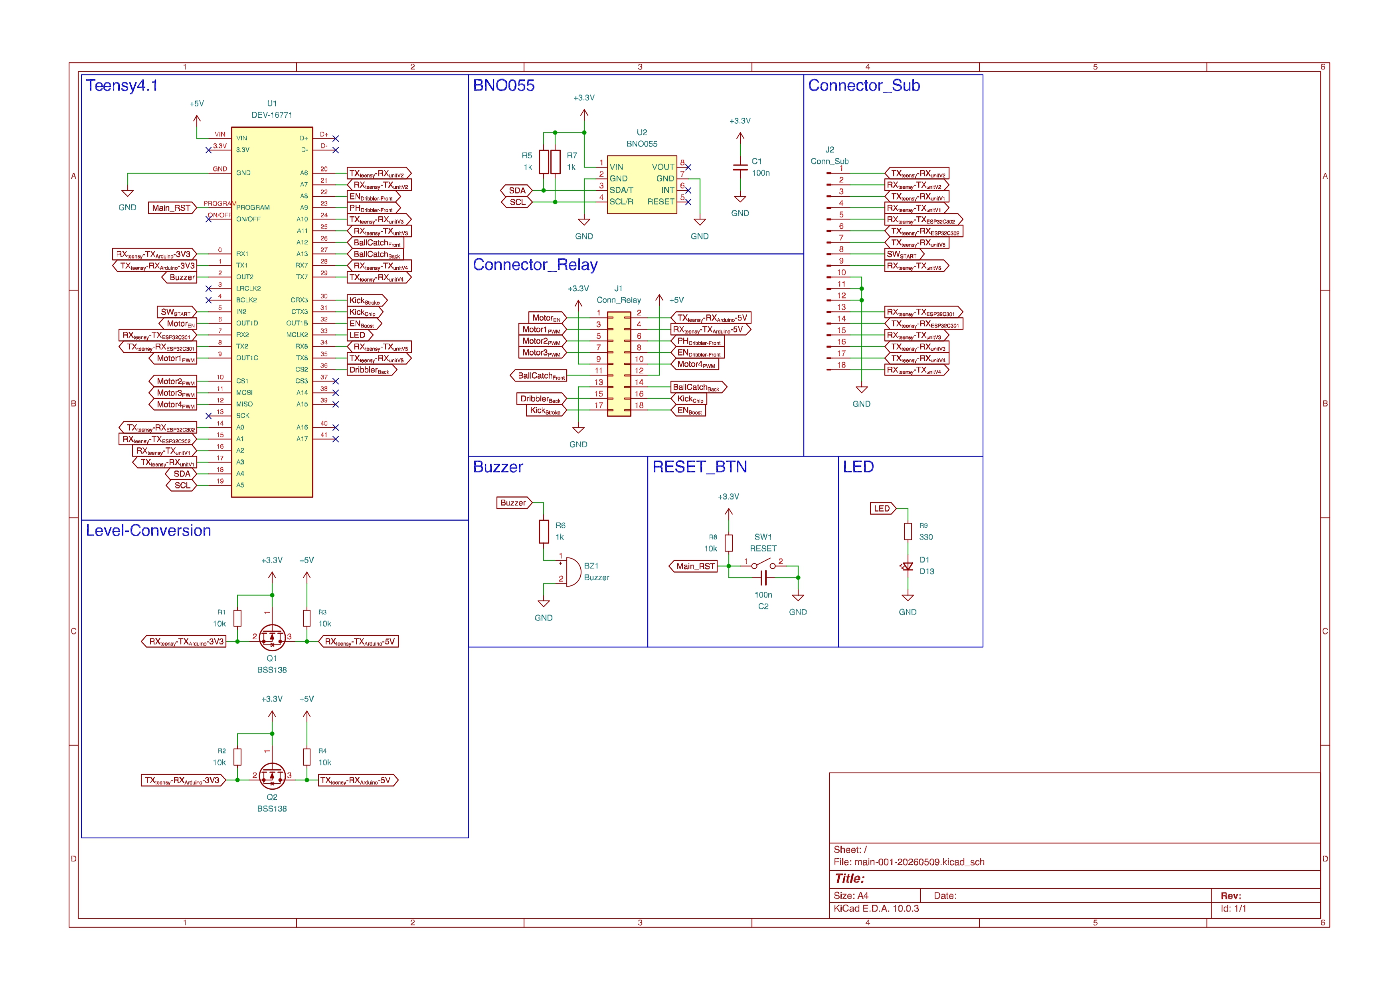
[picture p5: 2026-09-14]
circuit/main-001-20260509/main-schematic.jpg

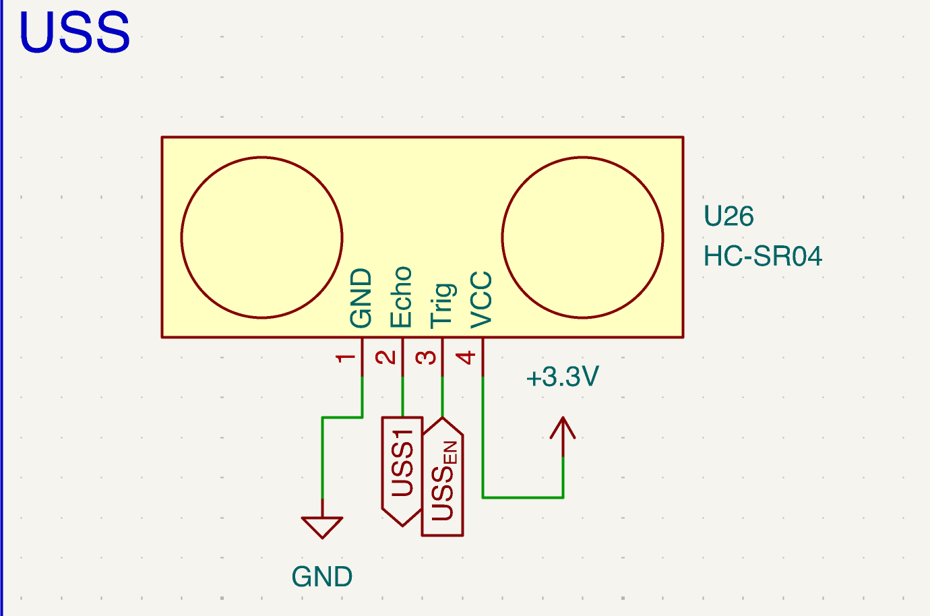
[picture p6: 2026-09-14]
circuit/sub-001-20260515/sub-schematic-uss.png

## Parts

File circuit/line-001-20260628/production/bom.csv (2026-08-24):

Designator | Footprint | Quantity | Value | LCSC Part #
C1, C10, C11, C12, C13, C14, C15, C16, C18, C2, C23, C24, C28, C3, C31, C32, C33, C34, C35, C36, C37, C38, C4, C5, C6, C7, C8, C9 | 0805 | 28 | 100n
C17, C19, C29, C30 | 0603 | 4 | 22p
C20 | 1206 | 1 | 100μ
C21, C22, C26, C27 | 0805 | 4 | 10u
D1, D10, D11, D12, D13, D14, D15, D16, D17, D18, D19, D2, D20, D21, D22, D23, D24, D25, D26, D27, D28, D29, D3, D30, D31, D32, D37, D38, D39, D4, D40, D5, D6, D7, D8, D9 | LED_D3.0mm | 36 | LED_Small
D41 | 0603 | 1 | LED1
D42 | 0603 | 1 | LED2
D43 | TSOT-23 | 1 | ~
D44 | 0603 | 1 | USB
J1 | AMASS_XT30U-M_1x02_P5.0mm_Vertical | 1 | Conn_01x02_Pin
J2 | Conn_01x02_Wire_Only | 1 | Conn_01x02_Pin
J3 | PinHeader_2x03_P2.54mm_Vertical | 1 | ICSP
J4 | USB_C_Receptacle_HCTL_HC-TYPE-C-16P-01A | 1 | USB_C_Receptacle_USB2.0_16P
Q1, Q10, Q11, Q12, Q13, Q14, Q15, Q16, Q17, Q18, Q19, Q2, Q20, Q21, Q22, Q23, Q24, Q25, Q26, Q27, Q28, Q29, Q3, Q30, Q31, Q32, Q37, Q38, Q39, Q4, Q40, Q5, Q6, Q7, Q8, Q9 | NJL7502L | 36 | Q_Photo_NPN_CE
R1, R10, R11, R12, R13, R14, R15, R16, R17, R18, R19, R2, R20, R21, R22, R23, R24, R25, R26, R27, R28, R29, R3, R30, R31, R32, R38, R4, R40, R5, R6, R7, R8, R81, R9 | 0805 | 35 | 10k
R41, R42, R43, R44, R45, R46, R47, R48, R49, R50, R51, R52, R53, R54, R55, R56, R57, R58, R59, R60, R61, R62, R63, R64, R65, R66, R67, R68, R69, R70, R71, R72, R77, R78, R79, R80 | 0805 | 36 | 75
R82, R89 | 0805 | 2 | 1M
R83, R84, R87, R88 | 0805 | 4 | 1K
R85, R86, R92 | 0805 | 3 | 330
R90, R91 | 0805 | 2 | 5.1k
R93 | 0805 | 1 | 4.7k
SW1 | TVBP06-B043C | 1 | SW_Push
SW2 | SS12D01G4 | 1 | SW_SPDT
U1, U10, U11, U12, U13, U14, U15, U16, U19, U2, U20, U3, U4, U5, U6, U7, U8, U9 | SOIC-8_3.9x4.9mm_P1.27mm | 18 | LM393DR
U17 | TQFP-100_14x14mm_P0.5mm | 1 | ATmega2560-16A
U18 | SOIC-16_3.9x9.9mm_P1.27mm | 1 | CH340G
Y1 | Crystal_SMD_SeikoEpson_FA238-4Pin_3.2x2.5mm | 1 | 16MHz
Y2 | Crystal_SMD_SeikoEpson_FA238V-4Pin_3.2x2.5mm | 1 | 12MHz

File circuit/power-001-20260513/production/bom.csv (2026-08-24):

Designator | Footprint | Quantity | Value | LCSC Part #
BZ1 | PKM13EPYH4000-A0 | 1 | Buzzer
C1 | CP_Radial_D8.0mm_P3.50mm | 1 | 470μ
C10, C11, C13, C5, C8 | 0805 | 5 | 10μ
C12, C2, C3 | 0805 | 3 | 100n
C6, C7, C9 | 0805 | 3 | 22μ
F1 | MF61NR_FUC-04 | 1 | 10A
J1 | Conn_01x02_Wire_Only | 1 | VIN
J2 | AMASS_XT30PW-F_1x02_P2.50mm_Horizontal | 1 | +5V_{Line}
J3 | AMASS_XT30PW-F_1x02_P2.50mm_Horizontal | 1 | Power
J4 | AMASS_XT30PW-F_1x02_P2.50mm_Horizontal | 1 | Logic
J5 | AMASS_XT30PW-F_1x02_P2.50mm_Horizontal | 1 | Sub_{Power}
J6 | PinHeader_1x02_P2.54mm_Horizontal | 1 | Sub_{Signal}
J7 | PinHeader_1x05_P1.00mm_Vertical | 1 | ICSP_{PIC12F683}
J8 | Conn_01x02_Wire_Only_SMD | 1 | ESC
Q1 | TSOT-23 | 1 | BSS138
Q2 | TO-252-2 | 1 | TJ60S04M3L
R10, R8 | 0805 | 2 | 1k
R11, R9 | 0805 | 2 | 330
R12, R13, R17 | 0805 | 3 | 1.2k
R14 | 0805 | 1 | 30k
R15, R19, R20, R21 | 0805 | 4 | 10k
R18 | 0805 | 1 | 100
R4, R5 | 0805 | 2 | 20k
R6, R7 | 0805 | 2 | 10
SW1, SW2 | 2MS1-T1-B4-M2-Q-E | 2 | SW_SPDT
SW4 | DS-850K-S-ON-K | 1 | Locker_SW
U1, U2 | OKL-T6-W12N-C | 2 | OKL-T/6-W12N-C
U3 | TO-252-2 | 1 | AZ1084-3.3
U5 | SOIC-8_3.9x4.9mm_P1.27mm | 1 | PIC12F683
U6 | SOT-223-3_TabPin2 | 1 | LM1117MP-3.3

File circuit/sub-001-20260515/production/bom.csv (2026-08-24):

Designator | Footprint | Quantity | Value | LCSC Part #
C1, C10, C11, C12, C13, C16, C19, C20, C23, C24, C26, C31, C32, C35, C36, C45, C46, C6, C7 | 0805 | 19 | 10μ
C14, C15, C2, C21, C22, C27, C28, C3, C33, C34, C37, C38, C43, C44, C8, C9 | 0805 | 16 | 10n
C17, C18, C29, C30, C39, C4, C40, C5 | 0805 | 8 | 1n
C25 | 0805 | 1 | 10u
C41, C42, C47, C48 | 0805 | 4 | 0.33μ
D1, D10, D2, D5, D6, D7, D8, D9 | LED_D3.0mm | 8 | IRLED
D3 | 0603 | 1 | 5V_{PWR}
D4 | 0603 | 1 | 3.3V_{PWR}
J1 | AFC01-S12FCA-00 | 1 | Conn_NeoPixel
J2 | PinSocket_1x02_P2.54mm_Vertical | 1 | Conn_01x02_Socket
J3 | AMASS_XT30U-M_1x02_P5.0mm_Vertical | 1 | Conn_Power
J4 | AFC01-S18FCA-00 | 1 | Conn_Main
Q1, Q2, Q3, Q4, Q5, Q6, Q7, Q8 | SOT-23 | 8 | BSS138
R1, R11, R12, R2, R23, R24, R33, R34 | 0805 | 8 | 18k
R10, R21, R22, R31, R32, R43, R44, R9 | 0805 | 8 | 1k
R13, R14, R25, R26, R3, R37, R38, R4 | 0805 | 8 | 1.5k
R15, R16 | 0805 | 2 | 330
R17, R18, R27, R28, R39, R40, R5, R6 | 0805 | 8 | 47
R19, R20, R29, R30, R41, R42, R7, R8 | 0805 | 8 | 100
R35, R36, R45, R46 | 0805 | 4 | 39k
R47, R48 | 0805 | 2 | 10k
U1, U10, U3, U6, U8 | NS-Tech_Grove_1x04_P2mm_Vertical | 5 | ~
U11, U14, U15, U2, U7 | SOT-223-3_TabPin2 | 5 | LM1117GS-3.3
U12, U13, U18, U19, U22, U23, U4, U5 | SOIC-8_3.9x4.9mm_P1.27mm | 8 | NE555DR
U16, U17 | XIAO-ESP32-C3-DIP | 2 | ~
U20, U21, U24, U25 | Vishay_MINICAST-3Pin | 4 | TSSP58038
U26, U27, U28, U29 | PinHeader_1x04_P2.54mm_Vertical | 4 | HC-SR04
U9 | SOT-223-3_TabPin2 | 1 | LM1117MP-3.3

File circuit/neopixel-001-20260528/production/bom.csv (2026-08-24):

Designator | Footprint | Quantity | Value | LCSC Part #
C1, C10, C11, C12, C13, C14, C15, C16, C17, C18, C19, C2, C3, C4, C5, C6, C7, C8, C9 | 0805 | 19 | 100n
D1, D10, D11, D12, D13, D14, D15, D16, D2, D3, D4, D5, D6, D7, D8, D9 | LED_WS2812B_PLCC4_5.0x5.0mm_P3.2mm | 16 | WS2812B
J1 | AFC01-S12FCA-00 | 1 | Conn_Sub
J2, J3 | JST_XH_B2B-XH-A_1x02_P2.50mm_Vertical | 2 | Conn_01x02_Pin
P1 | USB_C_Receptacle_GCT_USB4105-xx-A_16P_TopMnt_Horizontal | 1 | ESP32C3_{1}
P10 | USB_Type-C_Vertical_ C6332304 | 1 | UnitV3
P11 | USB_C_Receptacle_GCT_USB4105-xx-A_16P_TopMnt_Horizontal | 1 | UnitV4
P12 | USB_Type-C_Vertical_ C6332304 | 1 | UnitV4
P2 | USB_Type-C_Vertical_ C6332304 | 1 | ESP32C3_{1}
P3 | USB_C_Receptacle_GCT_USB4105-xx-A_16P_TopMnt_Horizontal | 1 | ESP32C3_{2}
P4 | USB_Type-C_Vertical_ C6332304 | 1 | ESP32C3_{2}
P5 | USB_C_Receptacle_GCT_USB4105-xx-A_16P_TopMnt_Horizontal | 1 | UnitV1
P6 | USB_Type-C_Vertical_ C6332304 | 1 | UnitV1
P7 | USB_C_Receptacle_GCT_USB4105-xx-A_16P_TopMnt_Horizontal | 1 | UnitV2
P8 | USB_Type-C_Vertical_ C6332304 | 1 | UnitV2
P9 | USB_C_Receptacle_GCT_USB4105-xx-A_16P_TopMnt_Horizontal | 1 | UnitV3
Q1, Q2, Q3 | TSOT-23 | 3 | BSS138
R1, R2 | 0805 | 2 | 1k
R10, R9 | 0805 | 2 | 500
R3, R5, R7 | 0805 | 3 | 10k
R4, R6, R8 | 0805 | 3 | 330
SW1, SW2, SW4 | ST-12-401FC-G | 3 | SW_SPST_LED
U1 | SSD1306_display_module | 1 | SSD1306
U2 | Aexit_0-50_Voltmeter | 1 | Aexit_0-50_Voltmeter
U3, U4, U5 | SOT-23-5_HandSoldering | 3 | 74AHC1G04

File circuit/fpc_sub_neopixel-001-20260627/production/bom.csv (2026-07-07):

Designator | Footprint | Quantity | Value | LCSC Part #
J1 | AFC01-S12FCA-00 | 1 | Conn_Sub
J2 | AFC01-S12FCA-00 | 1 | Conn_NeoPixel

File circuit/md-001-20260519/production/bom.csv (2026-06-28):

Designator | Footprint | Quantity | Value | LCSC Part #
C1, C2, C5, C6 | 0805 | 4 | 22n
C10, C11, C12, C13, C9 | 0805 | 5 | 100n
C14 | 1206 | 1 | 100μ
C3, C4, C7, C8 | 0805 | 4 | 220n
D1 | 0603 | 1 | MTR_PWR
D2 | 0603 | 1 | LGC_PWR
J1 | AMASS_XT30PW-F_1x02_P2.50mm_Horizontal | 1 | VIN-motor
J2 | PinSocket_1x03_P2.54mm_Vertical | 1 | Conn_Ball_Catch
J3 | PinHeader_2x08_P2.54mm_Horizontal | 1 | Conn_relay
R1, R10, R2, R9 | 0805 | 4 | 10k
R11, R13, R3, R5 | 0805 | 4 | NP
R12, R14, R4, R6 | 0805 | 4 | 20k
R15, R16, R17, R7, R8 | 0805 | 5 | 2.49k
R18 | 0805 | 1 | 330
U1, U2, U3, U4 | HTSSOP-16-1EP_4.4x5mm_P0.65mm_EP3.4x5mm_Mask2.66x2.46mm | 4 | ~

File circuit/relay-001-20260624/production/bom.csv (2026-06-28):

Designator | Footprint | Quantity | Value | LCSC Part #
J1 | PinHeader_1x03_P2.54mm_Vertical | 1 | Dribbler_{Back}
J10 | AMASS_XT30PW-M_1x02_P2.50mm_Horizontal | 1 | MD_{Power}
J11 | JST_XH_B2B-XH-A_1x02_P2.50mm_Vertical | 1 | Motor1
J12 | JST_XH_B2B-XH-A_1x02_P2.50mm_Vertical | 1 | Motor2
J13 | JST_XH_B2B-XH-A_1x02_P2.50mm_Vertical | 1 | Motor3
J14 | JST_XH_B2B-XH-A_1x02_P2.50mm_Vertical | 1 | Motor4
J15 | JST_XH_B2B-XH-A_1x02_P2.50mm_Vertical | 1 | Voltmeter
J2 | PinSocket_2x05_P2.54mm_Vertical | 1 | Kicker-Board
J3 | PinSocket_2x08_P2.54mm_Horizontal | 1 | MD_{Signal}
J4 | PinSocket_2x09_P2.54mm_Vertical | 1 | Main-Board
J5 | AMASS_XT30U-M_1x02_P5.0mm_Vertical | 1 | Power_{5V}
J6 | AMASS_XT30U-M_1x02_P5.0mm_Vertical | 1 | Power_{VCC}
J7 | AMASS_XT30U-M_1x02_P5.0mm_Vertical | 1 | Power_{Logic}
J8 | AMASS_XT30U-M_1x02_P5.0mm_Vertical | 1 | Line_{Power}
J9 | JST_XH_B2B-XH-A_1x02_P2.50mm_Vertical | 1 | Line_{UART}

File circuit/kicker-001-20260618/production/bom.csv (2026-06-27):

Designator | Footprint | Quantity | Value | LCSC Part #
C1 | 0805 | 1 | 47μ
C10 | 0805 | 1 | 220n
C11, C12, C3, C4, C5 | 0805 | 5 | 100n
C2, C6 | 0805 | 2 | 1μ
C7, C8 | 0805 | 2 | 10μ
C9 | 0805 | 1 | 22n
D1 | LED_D3.0mm | 1 | LED
D2 | CUHS20F60 | 1 | CUHS20F60
D3 | 0603 | 1 | PWR
D4 | 0603 | 1 | LGC
J1 | JST_XH_B2B-XH-A_1x02_P2.50mm_Vertical | 1 | Solenoid_{Stroke}
J2 | JST_XH_B2B-XH-A_1x02_P2.50mm_Vertical | 1 | Solenoid_{Chip}
J3 | JST_XH_B2B-XH-A_1x02_P2.50mm_Vertical | 1 | Drribler_{Front}
J4 | PinHeader_2x05_P2.54mm_Vertical | 1 | Conn_Relay
J6 | JST_XH_B2B-XH-A_1x02_P2.50mm_Vertical | 1 | Voltmeter
JP1, JP3 | SolderJumper-2_P1.3mm_Open_RoundedPad1.0x1.5mm | 2 | _{ON}
JP2, JP4 | SolderJumper-2_P1.3mm_Open_RoundedPad1.0x1.5mm | 2 | _{OFF}
L1 | SRC1317 | 1 | 33μ
Q1 | TSOT-23 | 1 | BSS138
Q2 | TO-252-2 | 1 | TJ15S06M3L
Q3 | NJL7502L | 1 | Q_Photo_CE
Q4, Q5 | TO-252-2 | 2 | MTB010N06RJ3
R1 | 0805 | 1 | 100
R10, R15 | 0805 | 2 | 2.49k
R11, R12 | 0805 | 2 | 100k
R13, R2, R3, R4, R5, R6 | 0805 | 6 | 10k
R14 | 0805 | 1 | NP
R16 | 0805 | 1 | 330
R17 | 0805 | 1 | 20k
R7 | 0805 | 1 | 1k
R8 | 0805 | 1 | 75
R9 | 0805 | 1 | 36k
U1, U4, U5, U7, U8 | SOT-23-5_HandSoldering | 5 | NOT
U10, U2, U9 | SO-5-6_4.55x3.7mm_P1.27mm | 3 | TLP2361
U11, U12 | SOT-23-5_HandSoldering | 2 | AND
U3 | TO-263-5_TabPin3 | 1 | XL6009E1
U6 | HTSSOP-16-1EP_4.4x5mm_P0.65mm_EP3.4x5mm_Mask2.66x2.46mm | 1 | DRV8874

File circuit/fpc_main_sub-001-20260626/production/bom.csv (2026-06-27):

Designator | Footprint | Quantity | Value | LCSC Part #
J1 | AFC01-S18FCA-00 | 1 | Conn_Sub
J2 | AFC01-S18FCA-00 | 1 | Conn_Main

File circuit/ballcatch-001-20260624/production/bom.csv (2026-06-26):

Designator | Footprint | Quantity | Value | LCSC Part #
D1 | LED_D3.0mm | 1 | OSR5JA3Z74A
J1 | PinHeader_1x03_P2.54mm_Vertical | 1 | Conn_BallCatch
Q1 | NJL7502L | 1 | NJL7502L
R1 | R_Axial_DIN0207_L6.3mm_D2.5mm_P7.62mm_Horizontal | 1 | 75
R2 | R_Axial_DIN0207_L6.3mm_D2.5mm_P7.62mm_Horizontal | 1 | 10k

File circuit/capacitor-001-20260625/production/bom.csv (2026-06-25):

Designator | Footprint | Quantity | Value | LCSC Part #
C1_2, C1, C2_2, C2, C3_2, C3, C4_2, C4 | CP_Radial_D12.5mm_P5.00mm | 8 | 1000u
J1_2, J1 | JST_XH_B2B-XH-A_1x02_P2.50mm_Vertical | 2 | Conn_Kicker

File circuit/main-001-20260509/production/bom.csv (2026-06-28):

Designator | Footprint | Quantity | Value | LCSC Part #
BZ1 | PKM13EPYH4000-A0 | 1 | Buzzer
C1, C2 | 0805 | 2 | 100n
D1 | 0603 | 1 | D13
J1 | PinHeader_2x09_P2.54mm_Vertical | 1 | Conn_Relay
J2 | AFC01-S18FCA-00 | 1 | Conn_Sub
Q1, Q2 | SOT-23 | 2 | BSS138
R1, R2, R3, R4, R8 | 0805 | 5 | 10k
R5, R6, R7 | 0805 | 3 | 1k
R9 | 0805 | 1 | 330
SW1 | TVBP06-B043C | 1 | RST
U1 | DEV-16771 | 1 | DEV-16771
U2 | BNO055 | 1 | BNO055

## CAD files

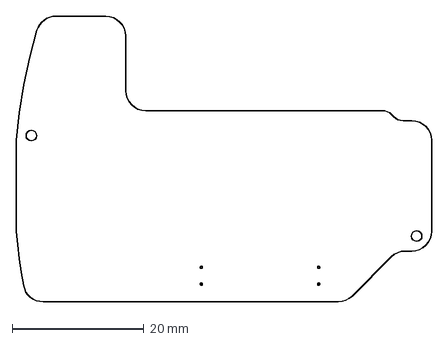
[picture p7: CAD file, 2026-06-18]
circuit/@sketches-dxf/Main-substrate_260618.dxf
63.0 x 43.3 mm

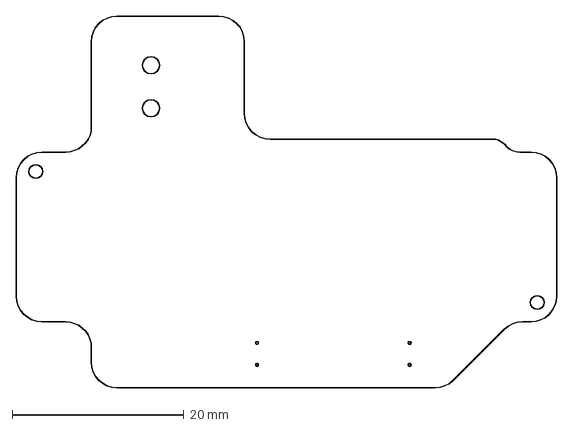
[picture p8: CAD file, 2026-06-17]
circuit/@sketches-dxf/Main-substrate_260617.dxf
63.0 x 43.3 mm

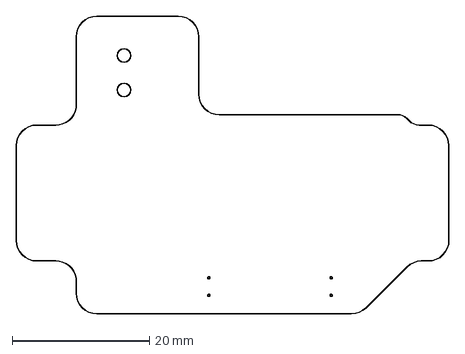
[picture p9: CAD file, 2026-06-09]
circuit/@sketches-dxf/Main-substrate_260608.dxf
63.0 x 43.3 mm

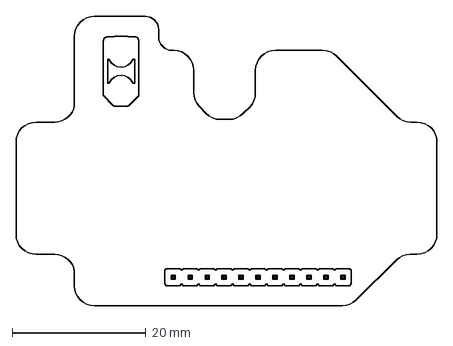
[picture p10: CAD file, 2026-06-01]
circuit/@sketches-dxf/Main-substrate_260601.dxf
63.0 x 43.3 mm

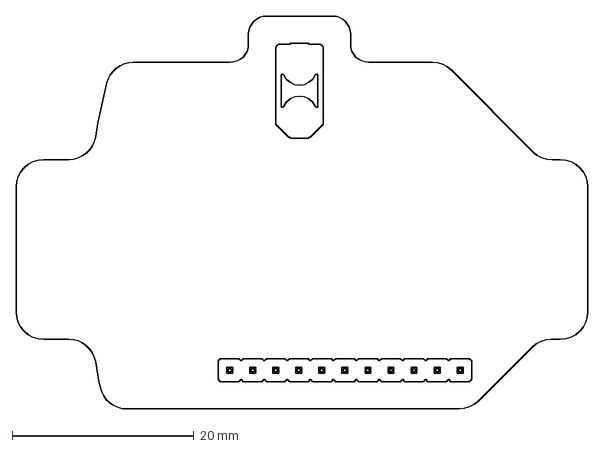
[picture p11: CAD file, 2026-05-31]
circuit/@sketches-dxf/Main-substrate_260531.dxf
63.0 x 43.3 mm

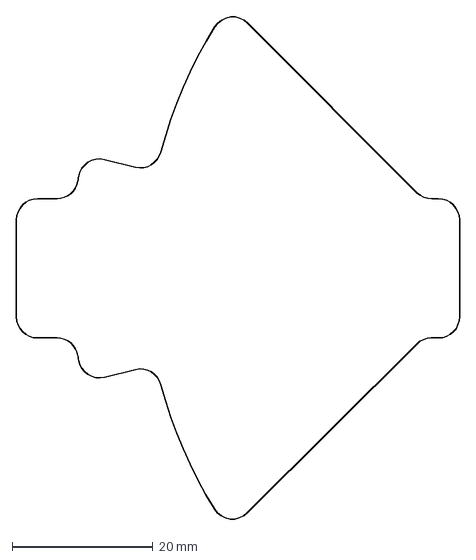
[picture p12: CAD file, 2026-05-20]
circuit/@sketches-dxf/Main-substrate_260520.dxf
63.0 x 71.5 mm

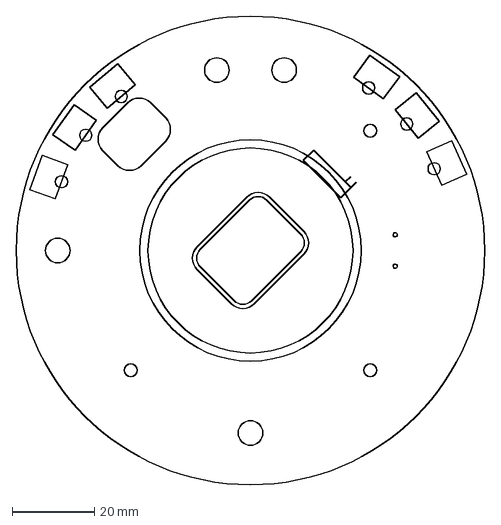
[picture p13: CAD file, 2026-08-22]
circuit/@sketches-dxf/Neopixel-substrate_260822.dxf
114.3 x 114.3 mm

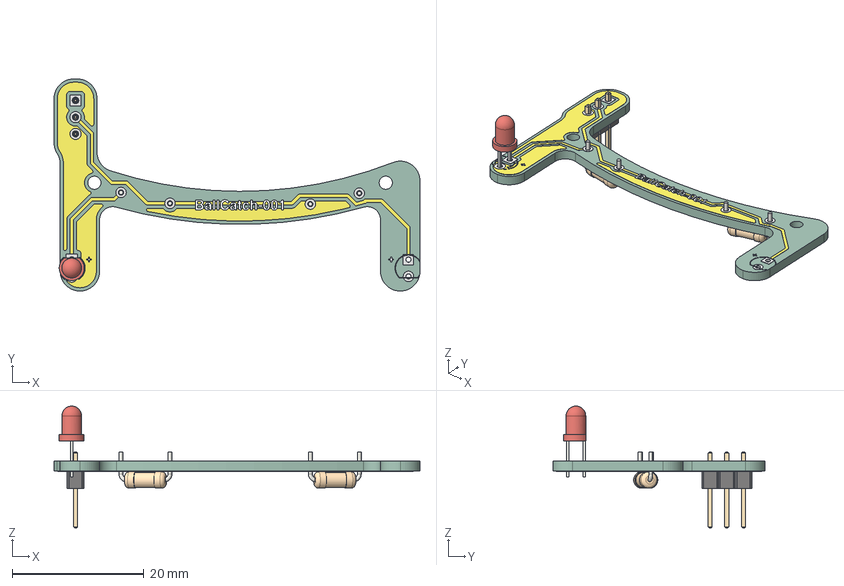
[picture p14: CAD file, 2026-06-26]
circuit/ballcatch-001-20260624/ballcatch-substrate.step
55.6 x 32.2 x 18.5 mm
LED_D3.0mm
R_Axial_DIN0207_L63mm_D25mm_P762mm_Horizontal x 2
PinHeader_1x03_P254mm_Vertical
ballcatch-001-20260624_copper
ballcatch-001-20260624_pad
ballcatch-001-20260624_silkscreen x 2
ballcatch-001-20260624_PCB

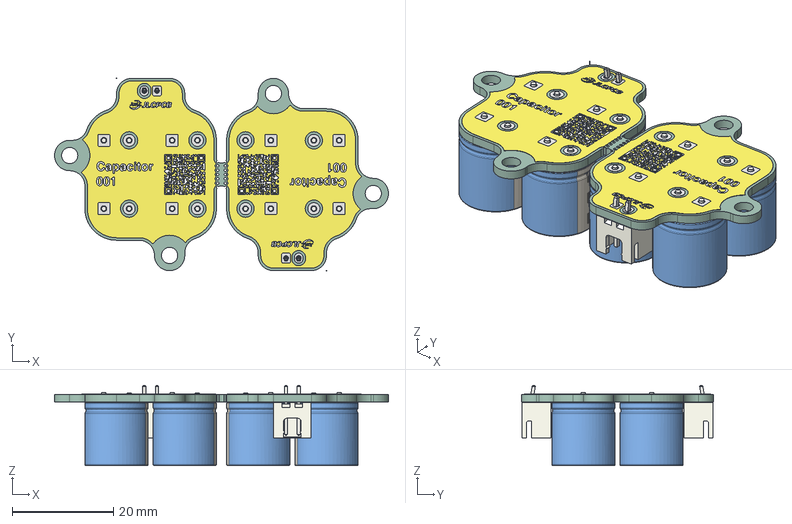
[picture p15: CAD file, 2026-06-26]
circuit/capacitor-001-20260625/capacitor-substrate.step
66.0 x 38.0 x 15.9 mm
JST_B2B_XH_A x 2
CP_Radial_D125mm_P500mm x 8
capacitor-001-20260625_copper
capacitor-001-20260625_pad
capacitor-001-20260625_silkscreen x 2
capacitor-001-20260625_PCB_1
capacitor-001-20260625_PCB_2
capacitor-001-20260625_PCB_3

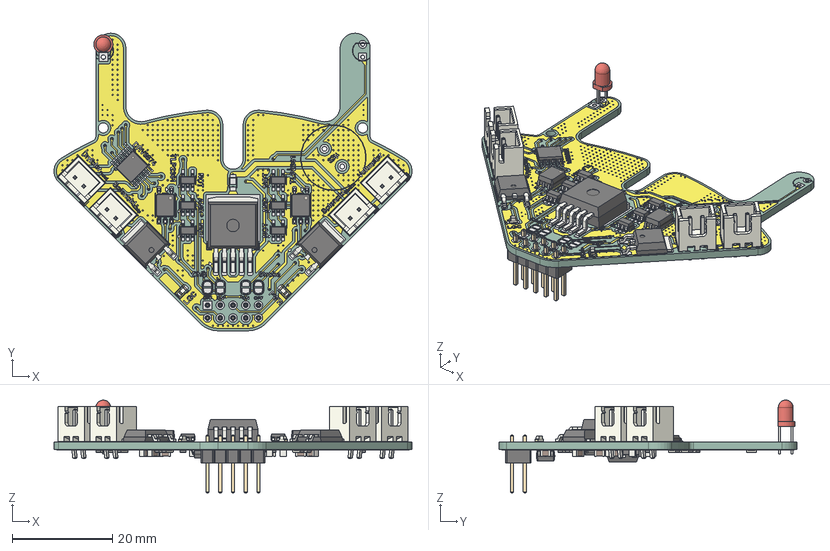
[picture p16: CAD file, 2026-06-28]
circuit/kicker-001-20260618/kicker-substrate.step
71.3 x 59.3 x 18.5 mm
SO-5-6_4.55x3.7mm_P1.27mm x 3
932d09b3-9c39-11ed-93f0-dde97e994e83_part x 3
932d09b4-9c39-11ed-93f0-dde97e994e83_part x 3
932d09b5-9c39-11ed-93f0-dde97e994e83_part x 3
a648ce37-9c39-11ed-93f0-dde97e994e83_part
a648ce38-9c39-11ed-93f0-dde97e994e83_part
a648ce39-9c39-11ed-93f0-dde97e994e83_part
LED_D3.0mm
SOT-23-5 x 7
JST_B2B_XH_A x 4
LED_0603_1608Metric x 2
HTSSOP-16-1EP_4.4x5mm_P0.65mm_EP3.4x5mm_Mask2.66x2.46mm
R_0805_2012Metric x 17
PinHeader_2x05_P254mm_Vertical
C_0805_2012Metric x 12
TSOT-23
kicker-001-20260618_copper
kicker-001-20260618_pad
kicker-001-20260618_via
kicker-001-20260618_silkscreen x 2
kicker-001-20260618_PCB

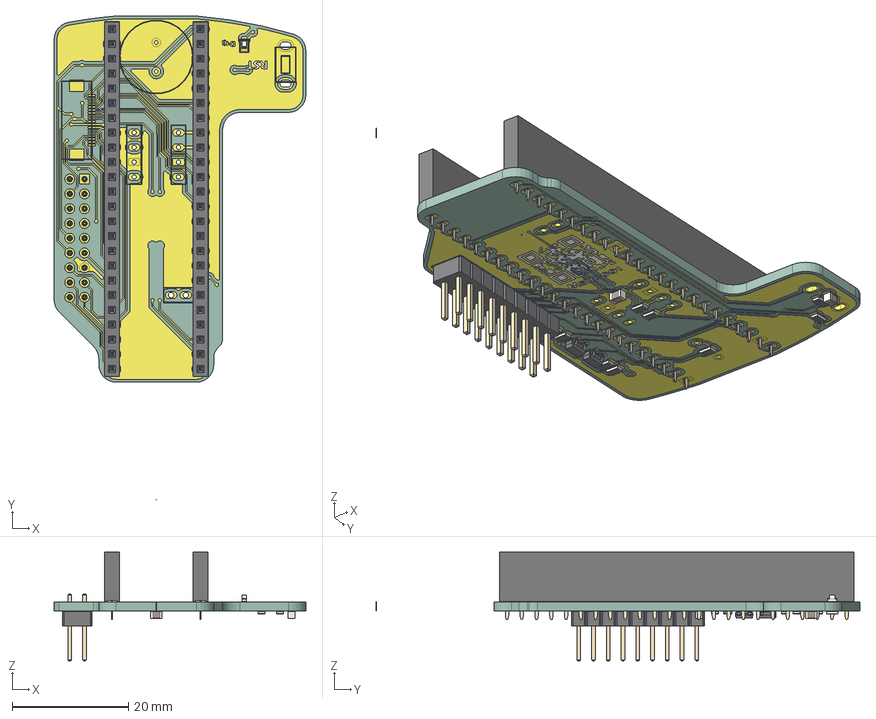
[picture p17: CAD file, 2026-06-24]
circuit/main-001-20260509/.step
43.3 x 83.2 x 18.7 mm
LED_0603_1608Metric
PinSocket_1x24_P2.54mm_Vertical x 2
SOT-23 x 2
R_0805_2012Metric x 9
C_0805_2012Metric x 2
PinHeader_2x09_P254mm_Vertical
main-001-20260509_copper
main-001-20260509_silkscreen x 2
main-001-20260509_PCB_1
main-001-20260509_PCB_2

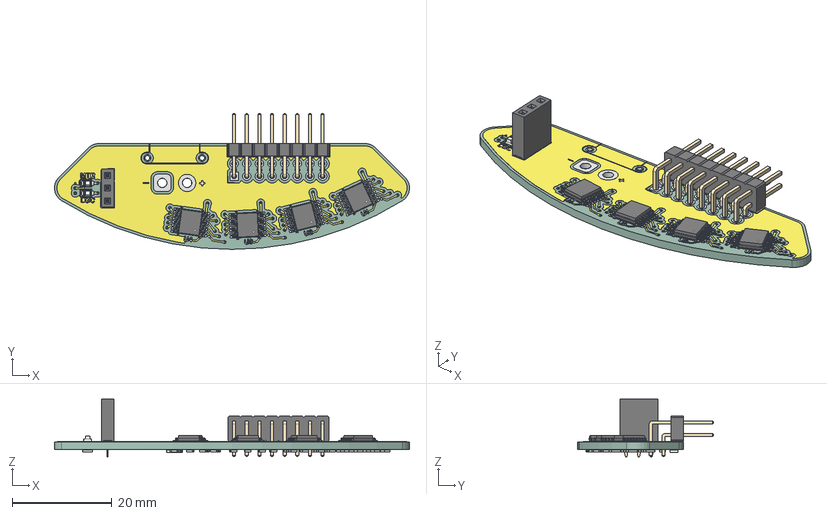
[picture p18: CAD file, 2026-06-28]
circuit/md-001-20260519/md-substrate.step
71.3 x 27.3 x 11.6 mm
PinHeader_2x08_P254mm_Horizontal
HTSSOP-16-1EP_4.4x5mm_P0.65mm_EP3.4x5mm_Mask2.66x2.46mm x 4
LED_0603_1608Metric x 2
PinSocket_1x03_P2.54mm_Vertical
R_0805_2012Metric x 31
R_1206_3216Metric
md-001-20260519_copper
md-001-20260519_pad
md-001-20260519_via
md-001-20260519_silkscreen x 2
md-001-20260519_PCB

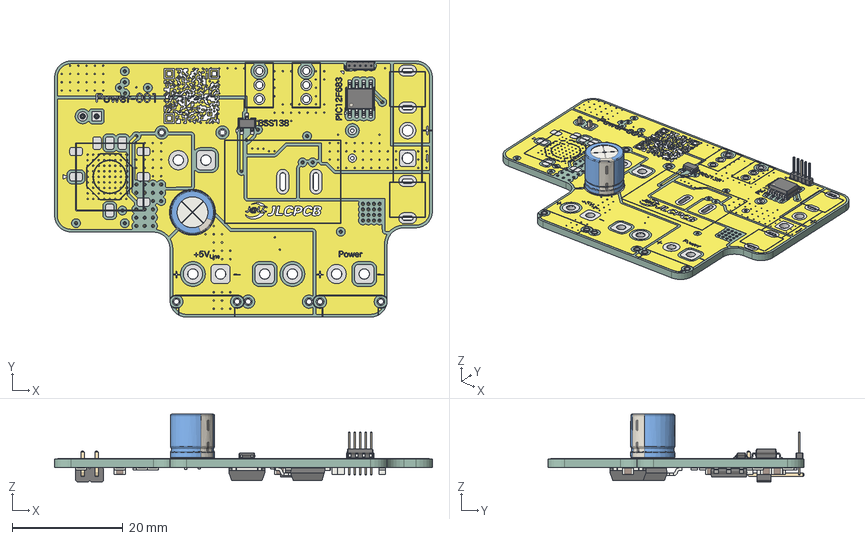
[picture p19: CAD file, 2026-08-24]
circuit/power-001-20260513/power-substrate.step
68.4 x 46.4 x 12.2 mm
PinHeader_1x05_P100mm_Vertical
SOIC-8_3.9x4.9mm_P1.27mm
CP_Radial_D80mm_P350mm
TSOT-23
C_0805_2012Metric x 11
R_0805_2012Metric x 17
932d09b3-9c39-11ed-93f0-dde97e994e83_part x 2
932d09b4-9c39-11ed-93f0-dde97e994e83_part x 2
932d09b5-9c39-11ed-93f0-dde97e994e83_part x 2
PinHeader_1x02_P254mm_Horizontal
SOT-223
power-001-20260513_copper
power-001-20260513_pad
power-001-20260513_via
power-001-20260513_silkscreen x 2
power-001-20260513_PCB

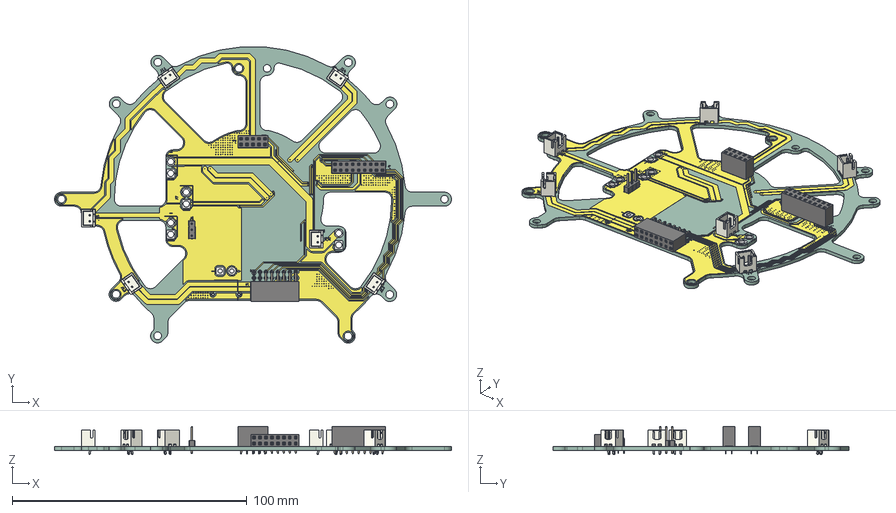
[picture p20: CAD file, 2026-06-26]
circuit/relay-001-20260624/.step
169.0 x 126.1 x 11.9 mm
JST_B2B_XH_A x 6
PinSocket_2x09_P2.54mm_Vertical
PinSocket_2x08_P2.54mm_Horizontal
PinHeader_1x03_P254mm_Vertical
PinSocket_2x05_P2.54mm_Vertical
relay-001-20260624_copper
relay-001-20260624_pad
relay-001-20260624_via
relay-001-20260624_silkscreen
relay-001-20260624_PCB

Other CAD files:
fabrication/3D Print/Adventure 5M Fuse1+/115_motor-mount.stl
fabrication/3D Print/JLCPCB/tipkick-plate.step
fabrication/CNC/Shitaita_v1_260522.dxf
circuit/@sketches-dxf/BackCatch-substrate_260612.dxf
circuit/@sketches-dxf/BackCatch-substrate_260623.dxf
circuit/@sketches-dxf/BackCatch-substrate_260624.dxf
circuit/@sketches-dxf/Kikker-substrate_260531.dxf
circuit/@sketches-dxf/Kikker-substrate_260608.dxf
circuit/@sketches-dxf/Kikker-substrate_260623.dxf
circuit/@sketches-dxf/Kikker-substrate_260624.dxf
circuit/@sketches-dxf/Line-substrate_260521.dxf
circuit/@sketches-dxf/Line-substrate_260623.dxf
circuit/@sketches-dxf/Line-substrate_260813.dxf
circuit/@sketches-dxf/Line-substrate_260814.dxf
circuit/@sketches-dxf/Line-substrate_260818.dxf
circuit/@sketches-dxf/MD-substrate_260520.dxf
circuit/@sketches-dxf/MD-substrate_260531.dxf
circuit/@sketches-dxf/MD-substrate_260604.dxf
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

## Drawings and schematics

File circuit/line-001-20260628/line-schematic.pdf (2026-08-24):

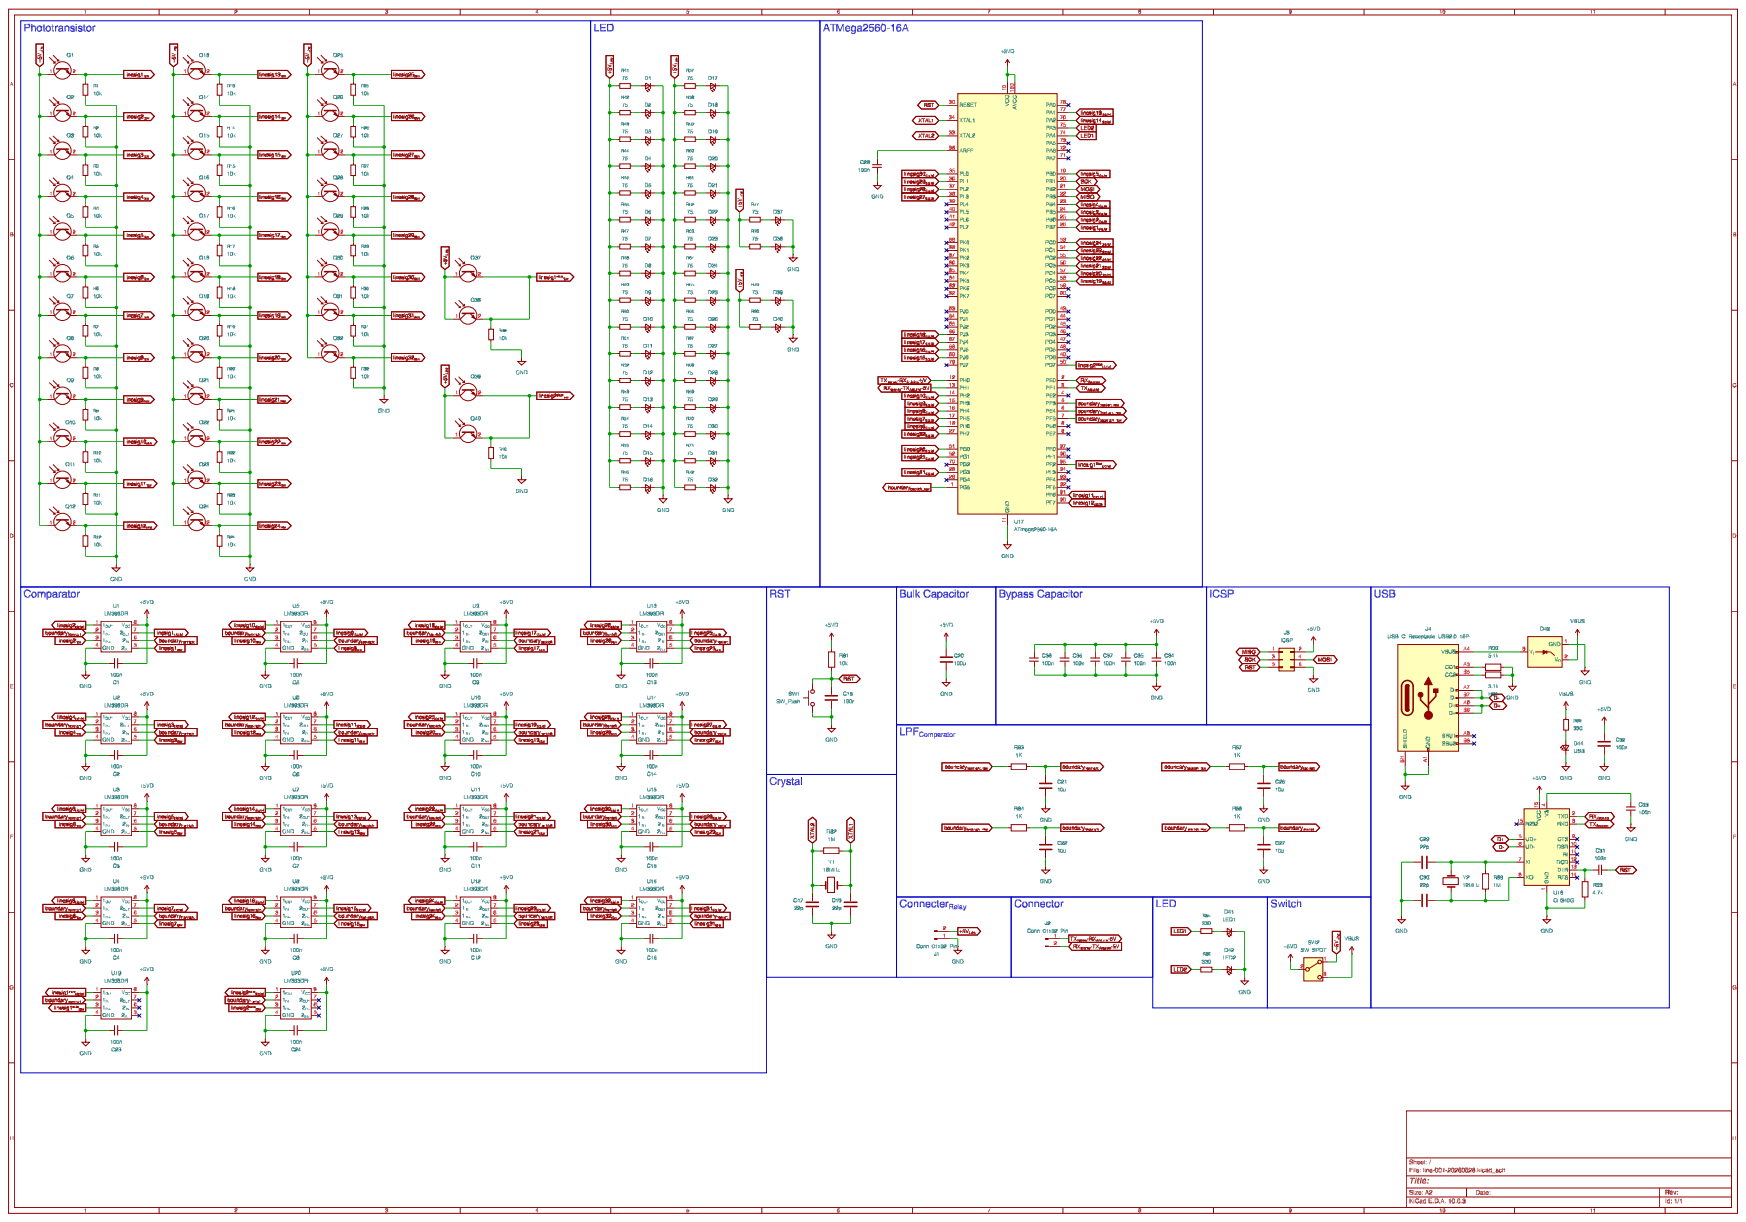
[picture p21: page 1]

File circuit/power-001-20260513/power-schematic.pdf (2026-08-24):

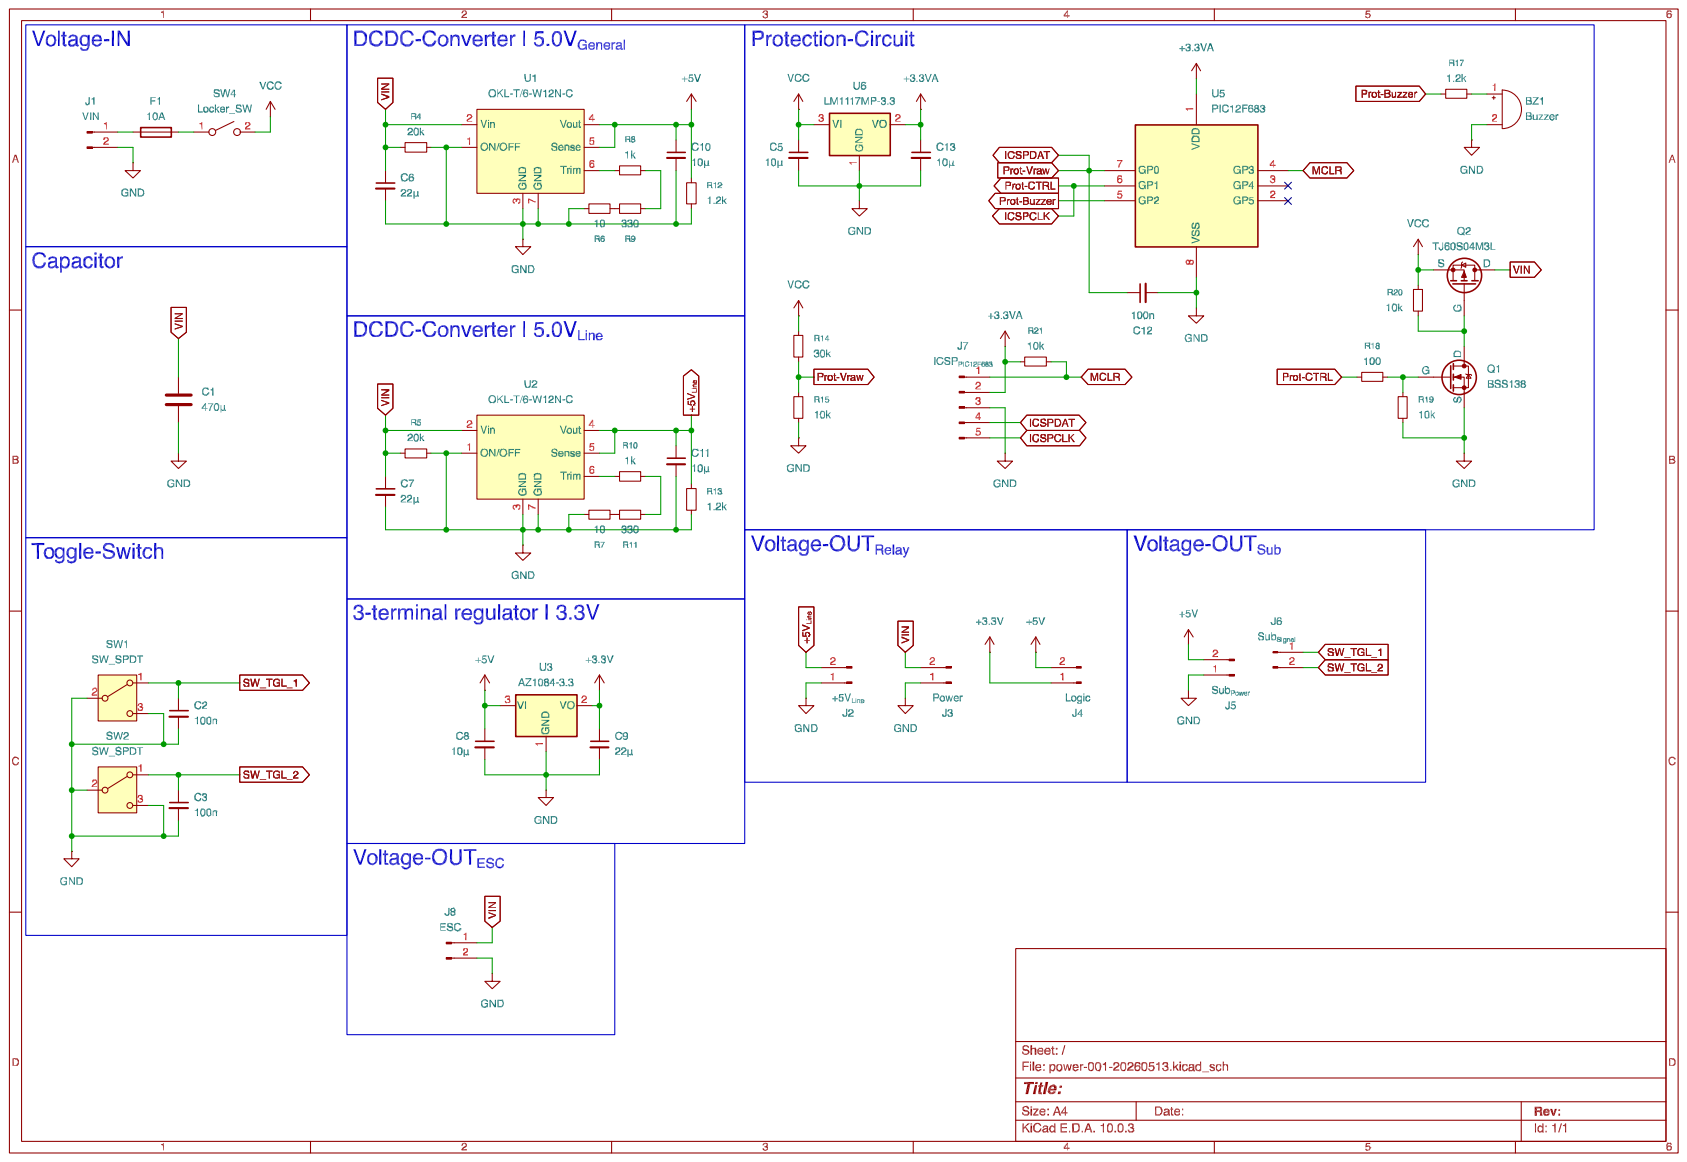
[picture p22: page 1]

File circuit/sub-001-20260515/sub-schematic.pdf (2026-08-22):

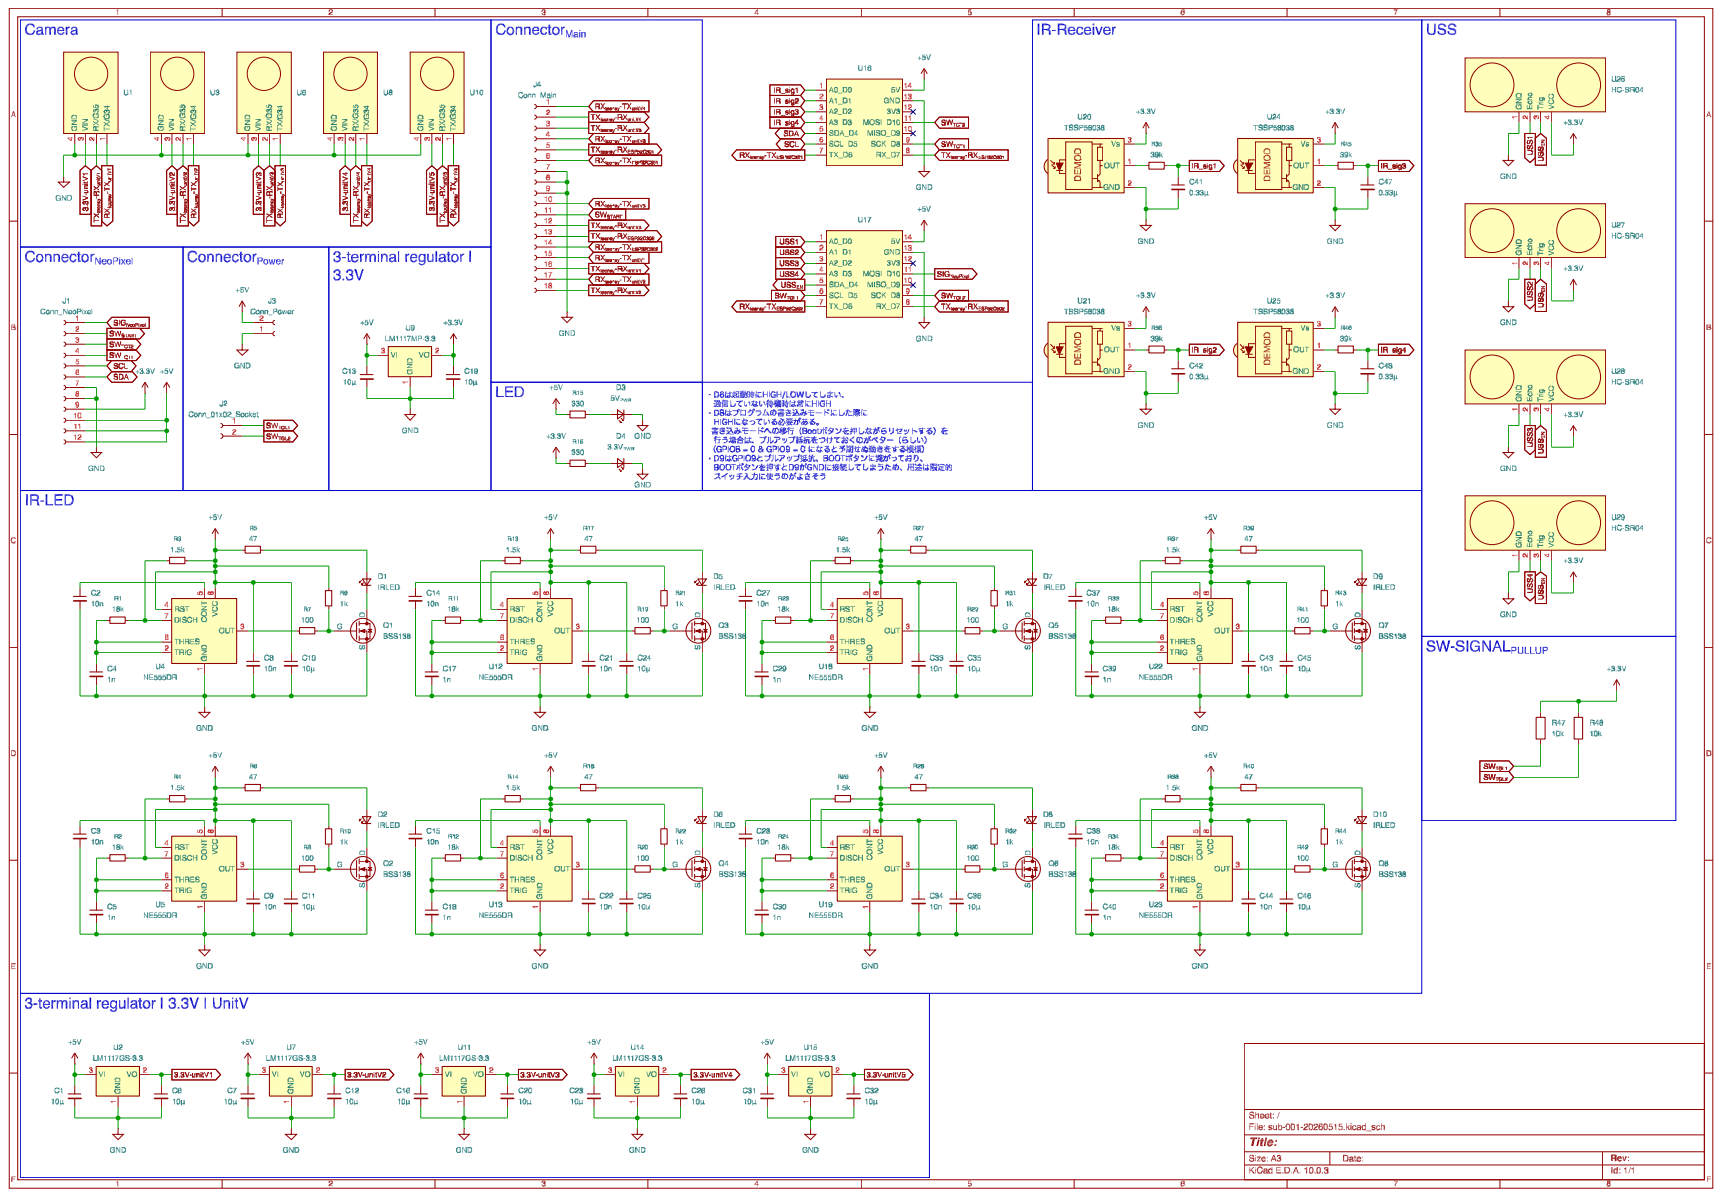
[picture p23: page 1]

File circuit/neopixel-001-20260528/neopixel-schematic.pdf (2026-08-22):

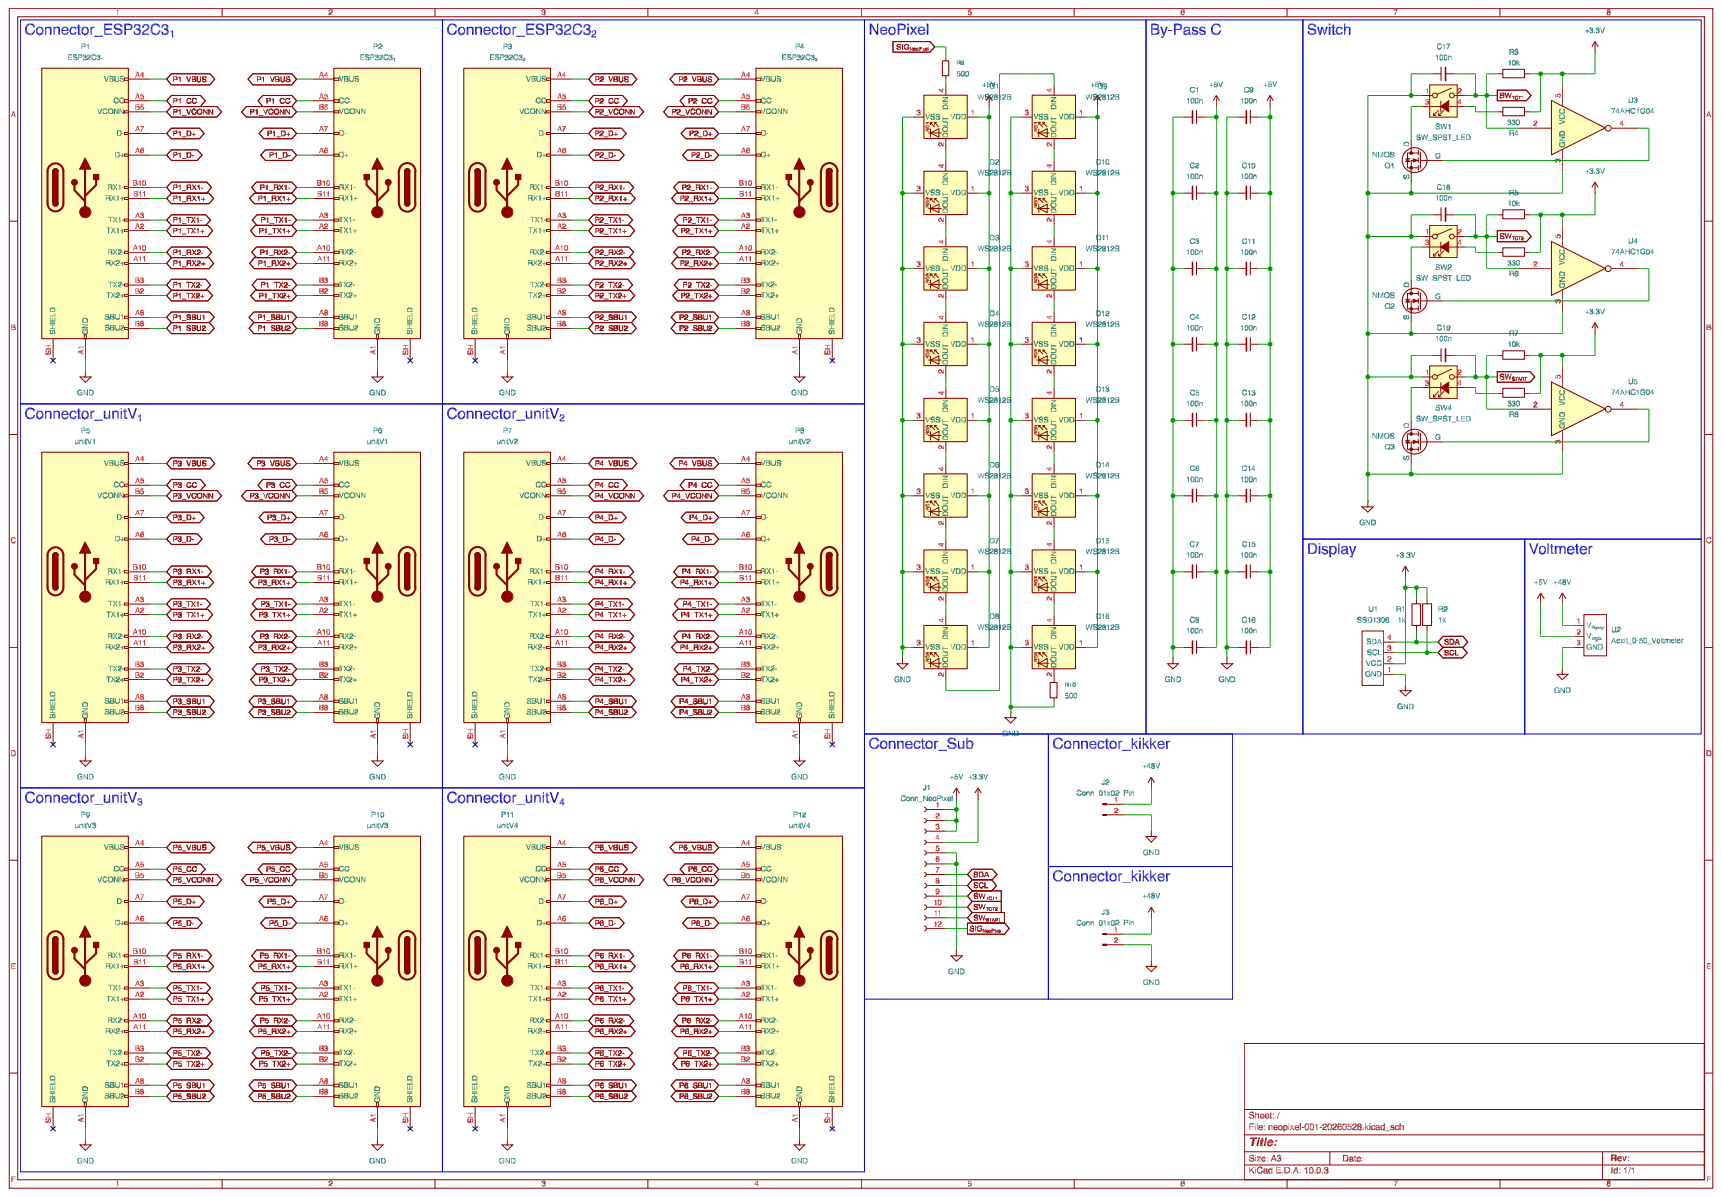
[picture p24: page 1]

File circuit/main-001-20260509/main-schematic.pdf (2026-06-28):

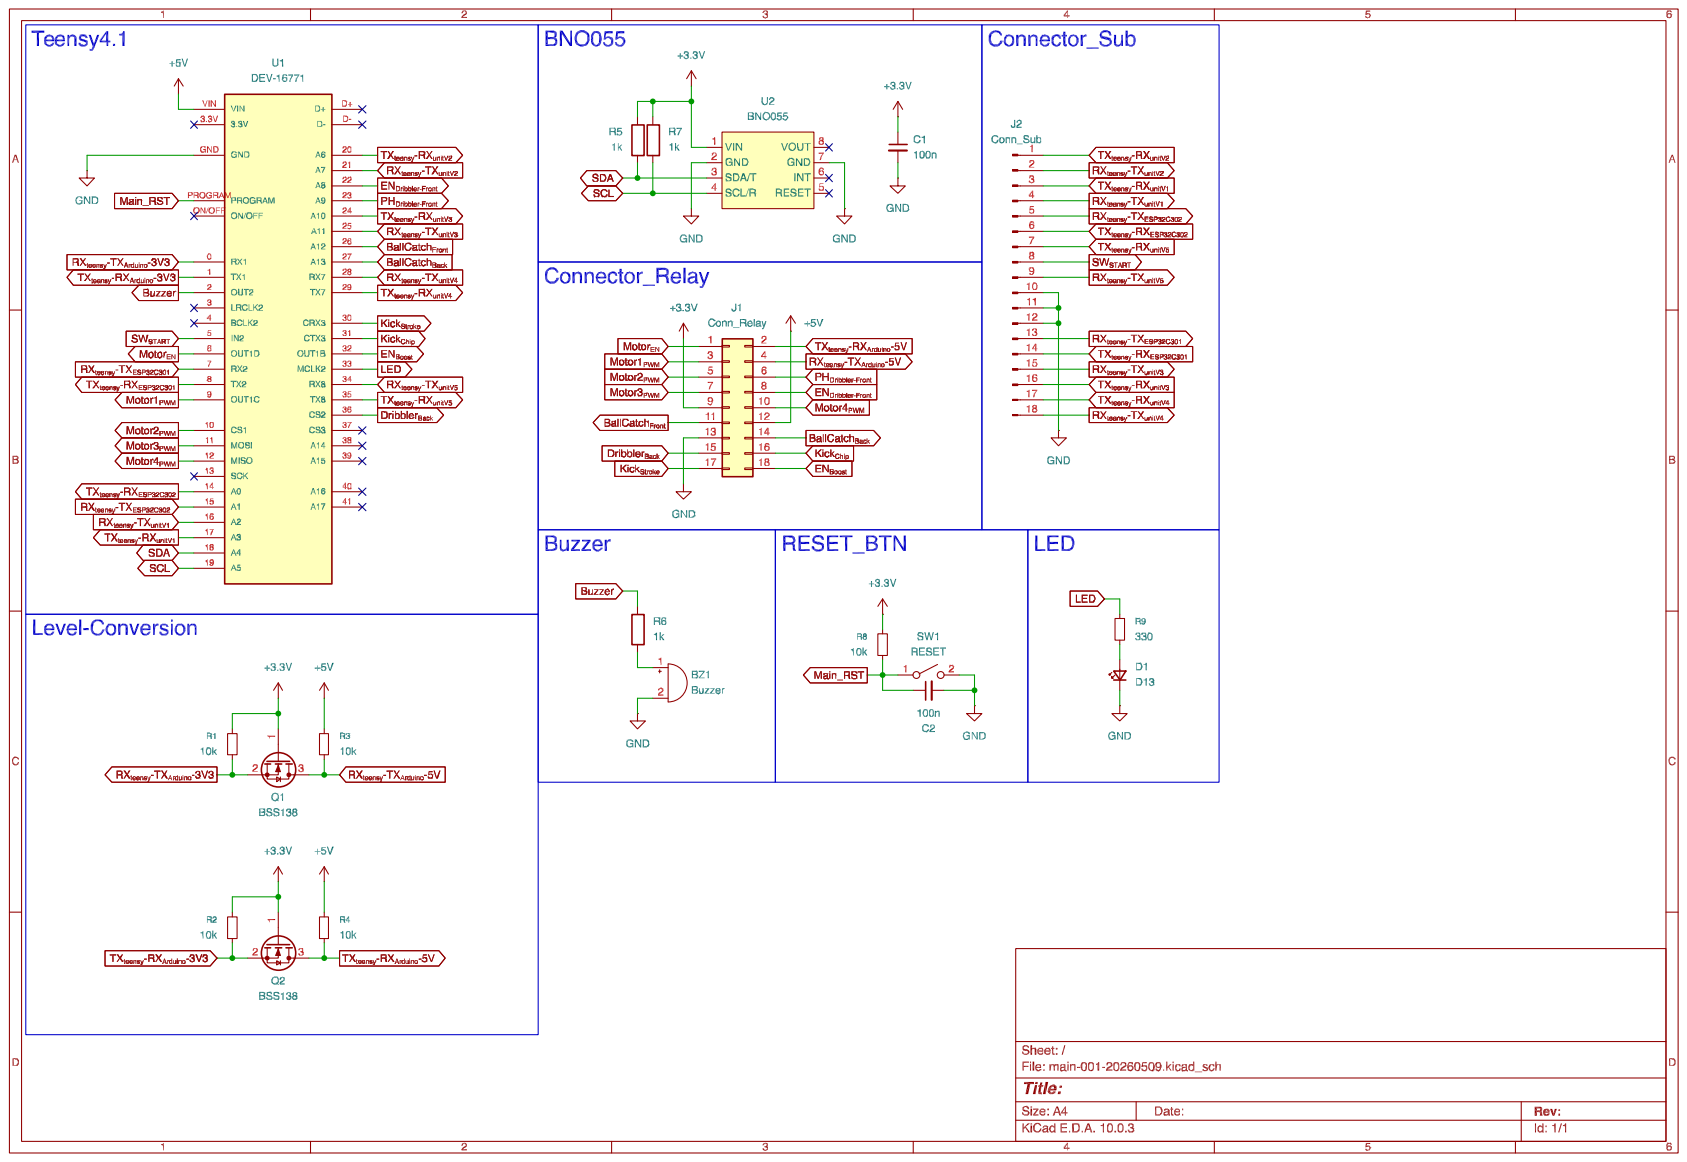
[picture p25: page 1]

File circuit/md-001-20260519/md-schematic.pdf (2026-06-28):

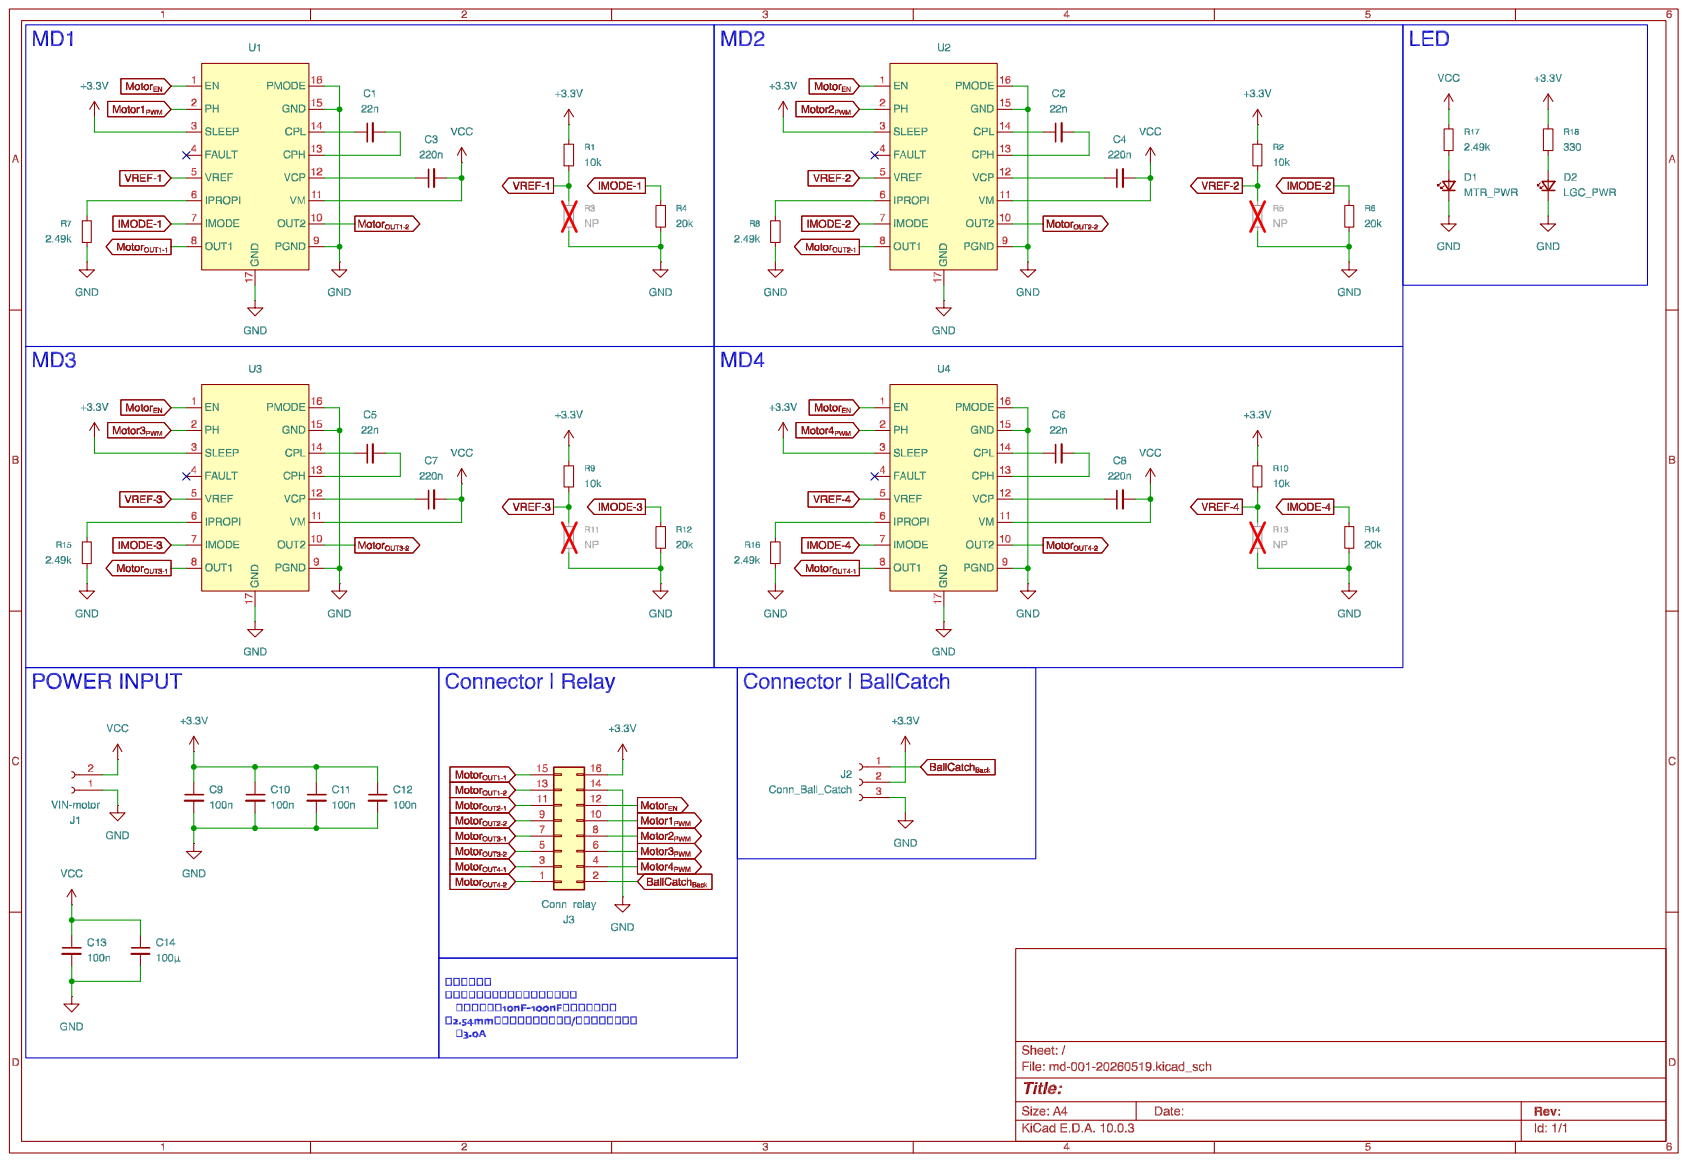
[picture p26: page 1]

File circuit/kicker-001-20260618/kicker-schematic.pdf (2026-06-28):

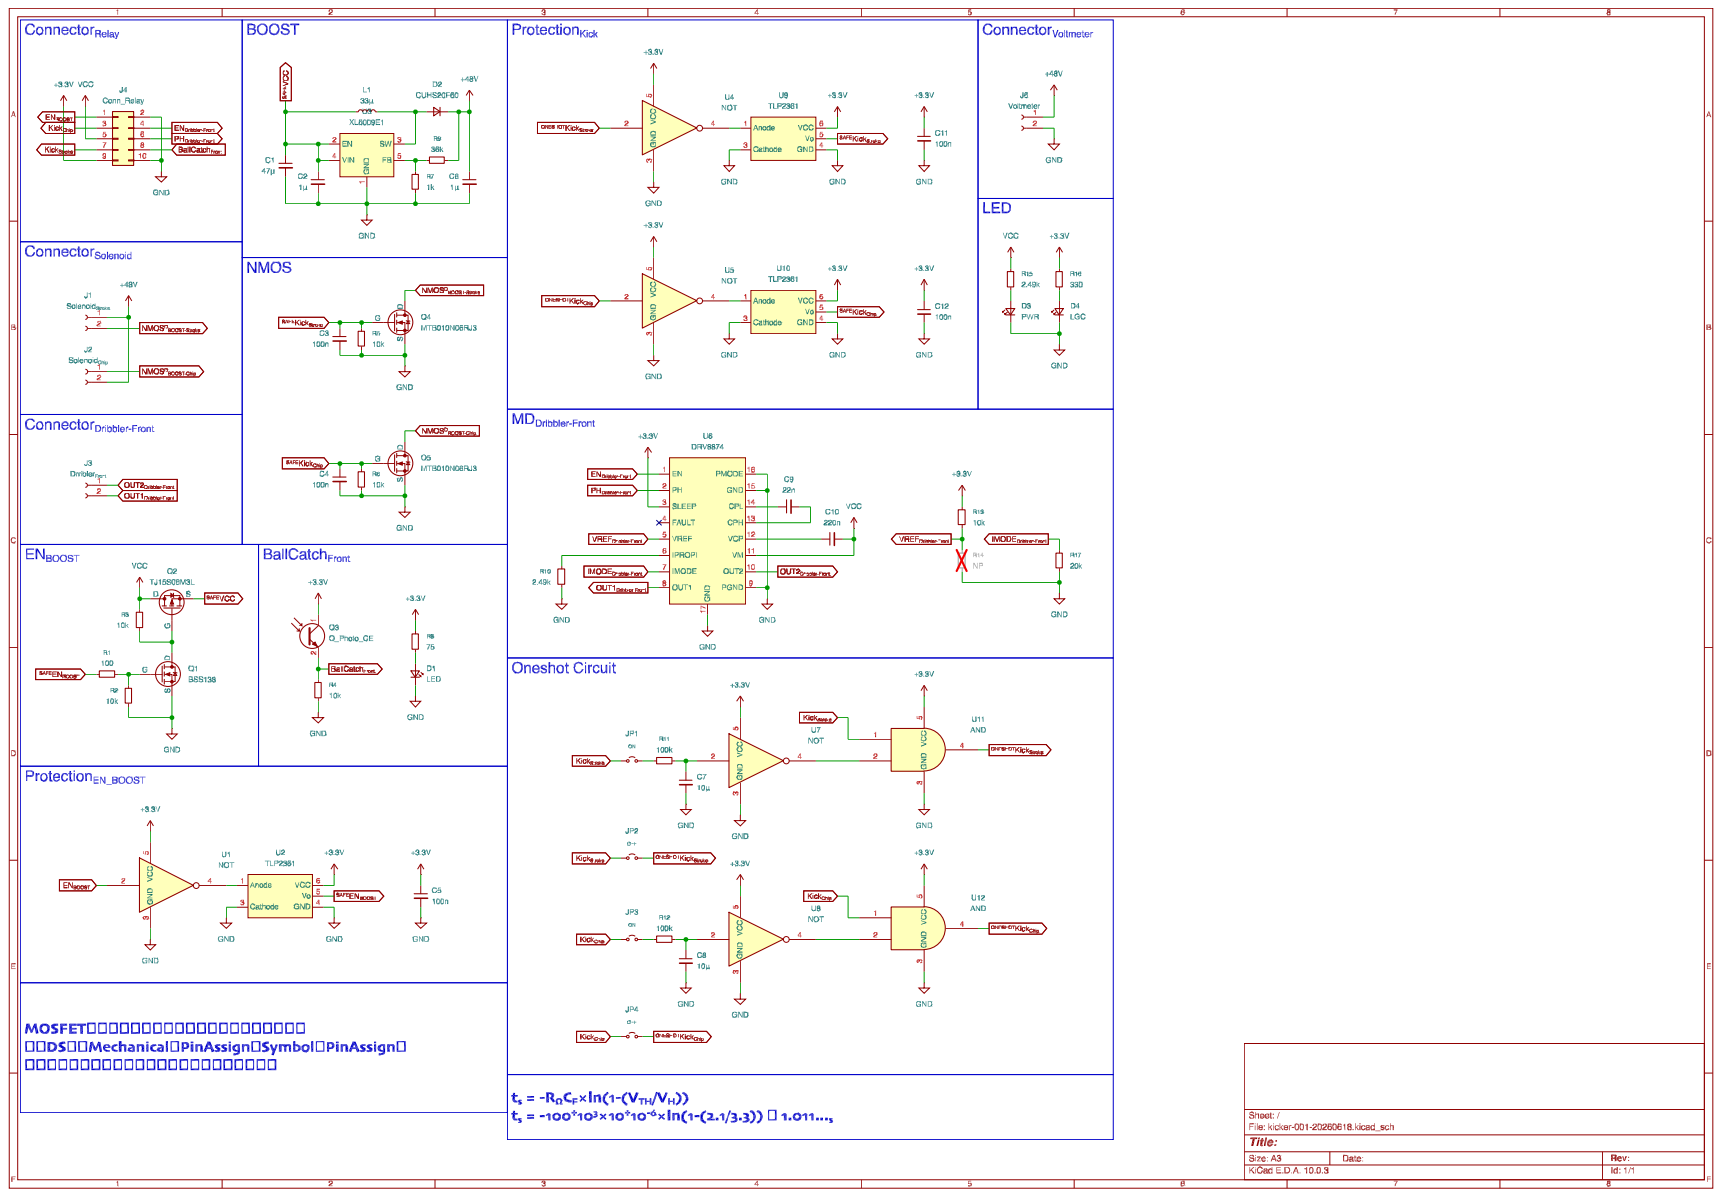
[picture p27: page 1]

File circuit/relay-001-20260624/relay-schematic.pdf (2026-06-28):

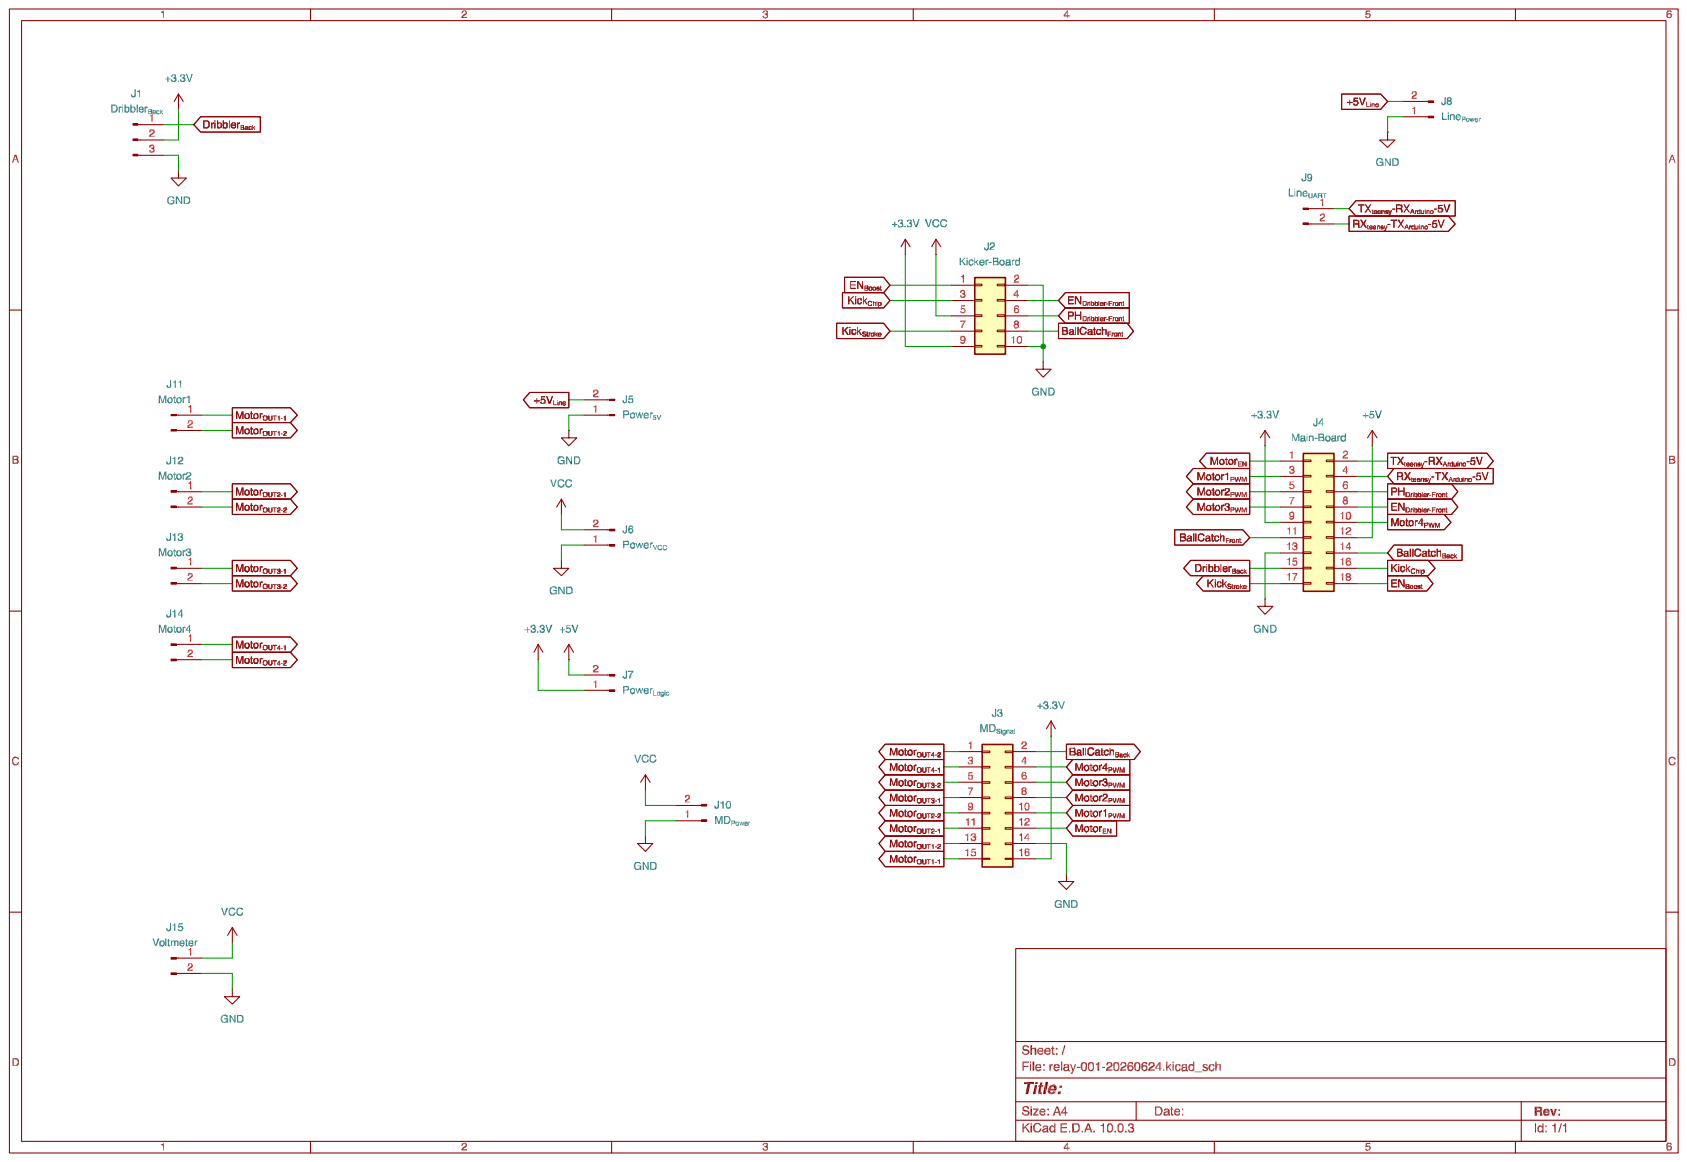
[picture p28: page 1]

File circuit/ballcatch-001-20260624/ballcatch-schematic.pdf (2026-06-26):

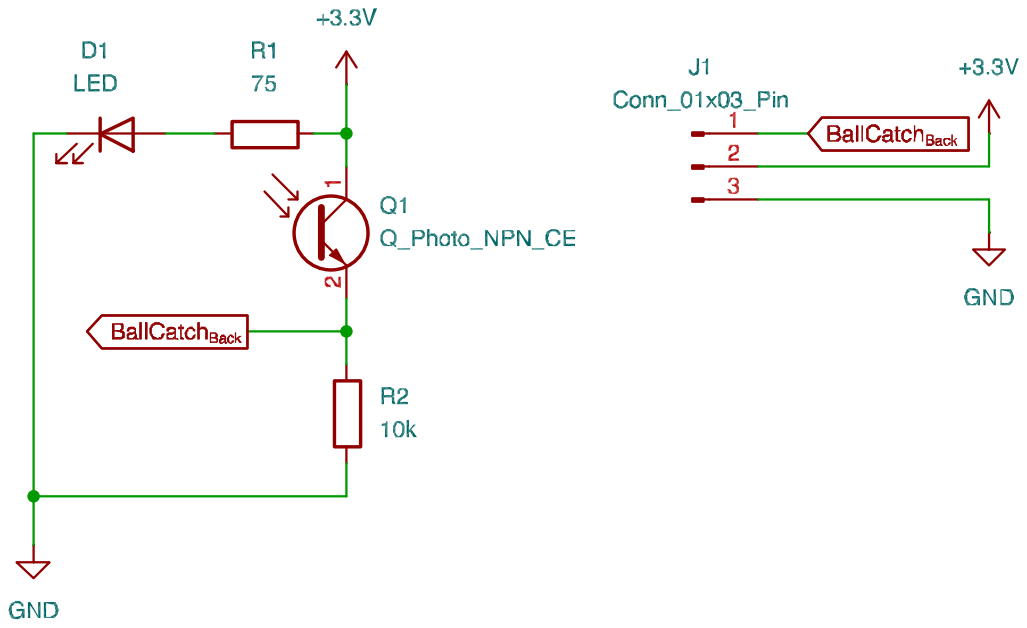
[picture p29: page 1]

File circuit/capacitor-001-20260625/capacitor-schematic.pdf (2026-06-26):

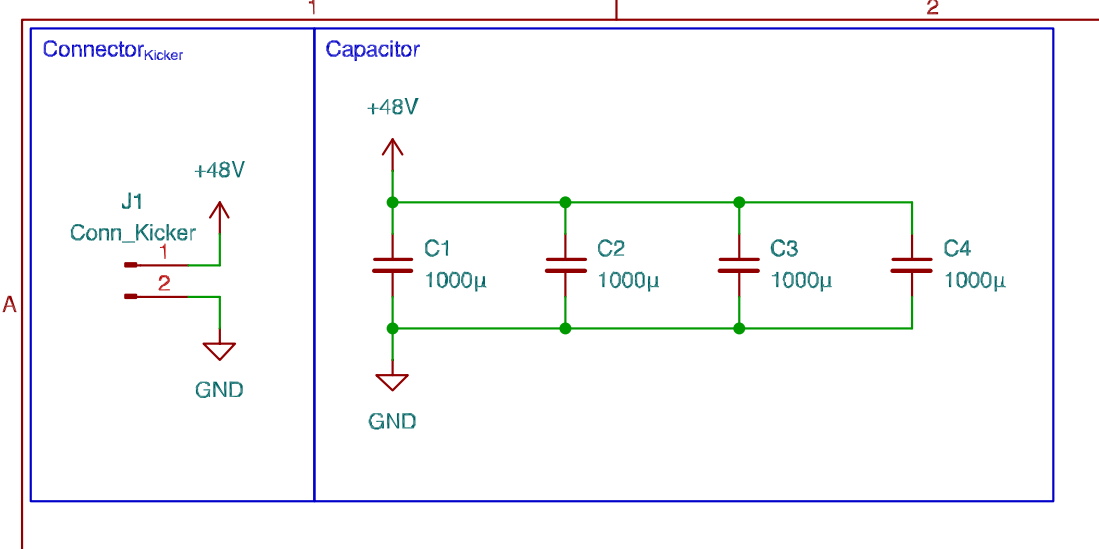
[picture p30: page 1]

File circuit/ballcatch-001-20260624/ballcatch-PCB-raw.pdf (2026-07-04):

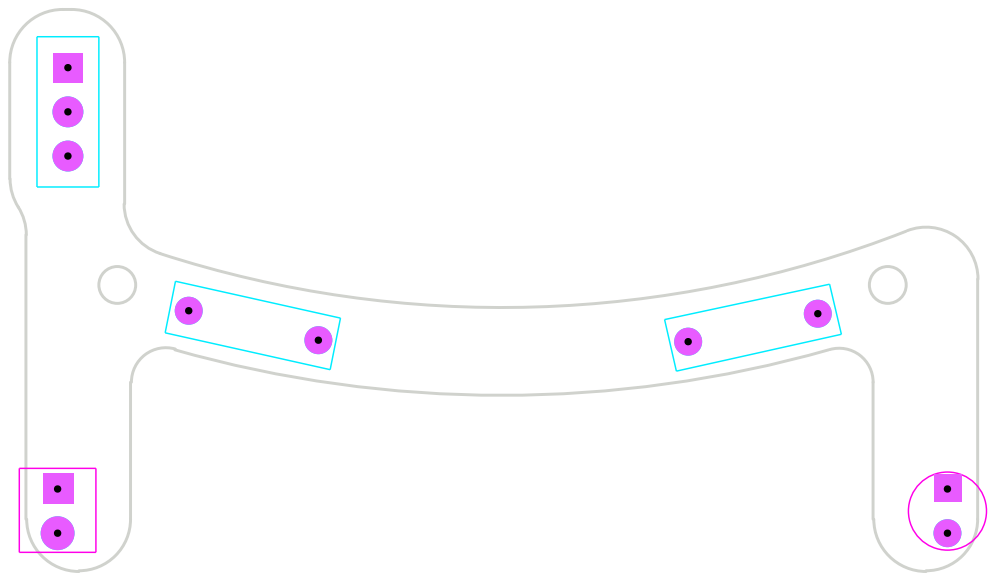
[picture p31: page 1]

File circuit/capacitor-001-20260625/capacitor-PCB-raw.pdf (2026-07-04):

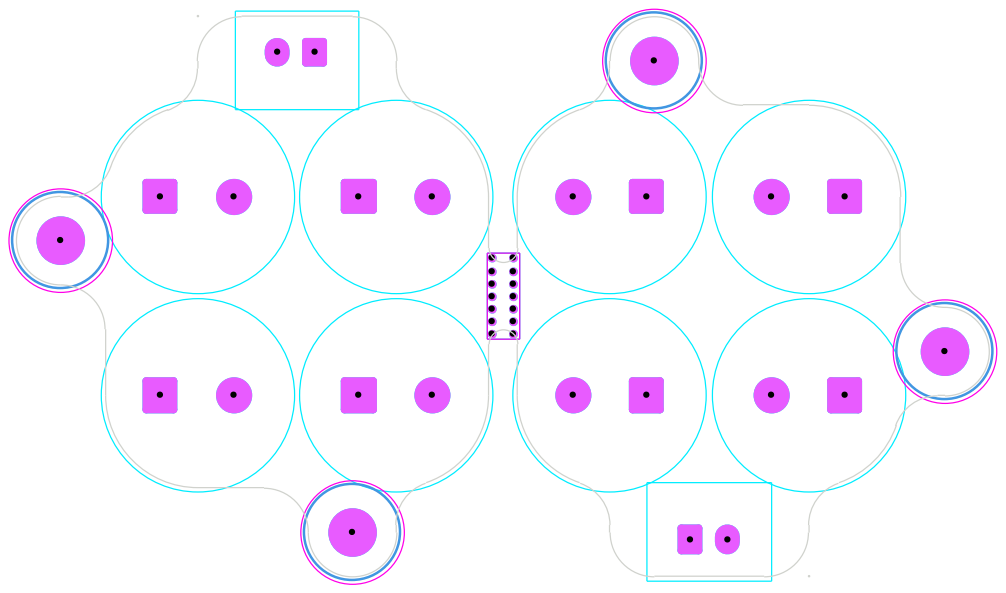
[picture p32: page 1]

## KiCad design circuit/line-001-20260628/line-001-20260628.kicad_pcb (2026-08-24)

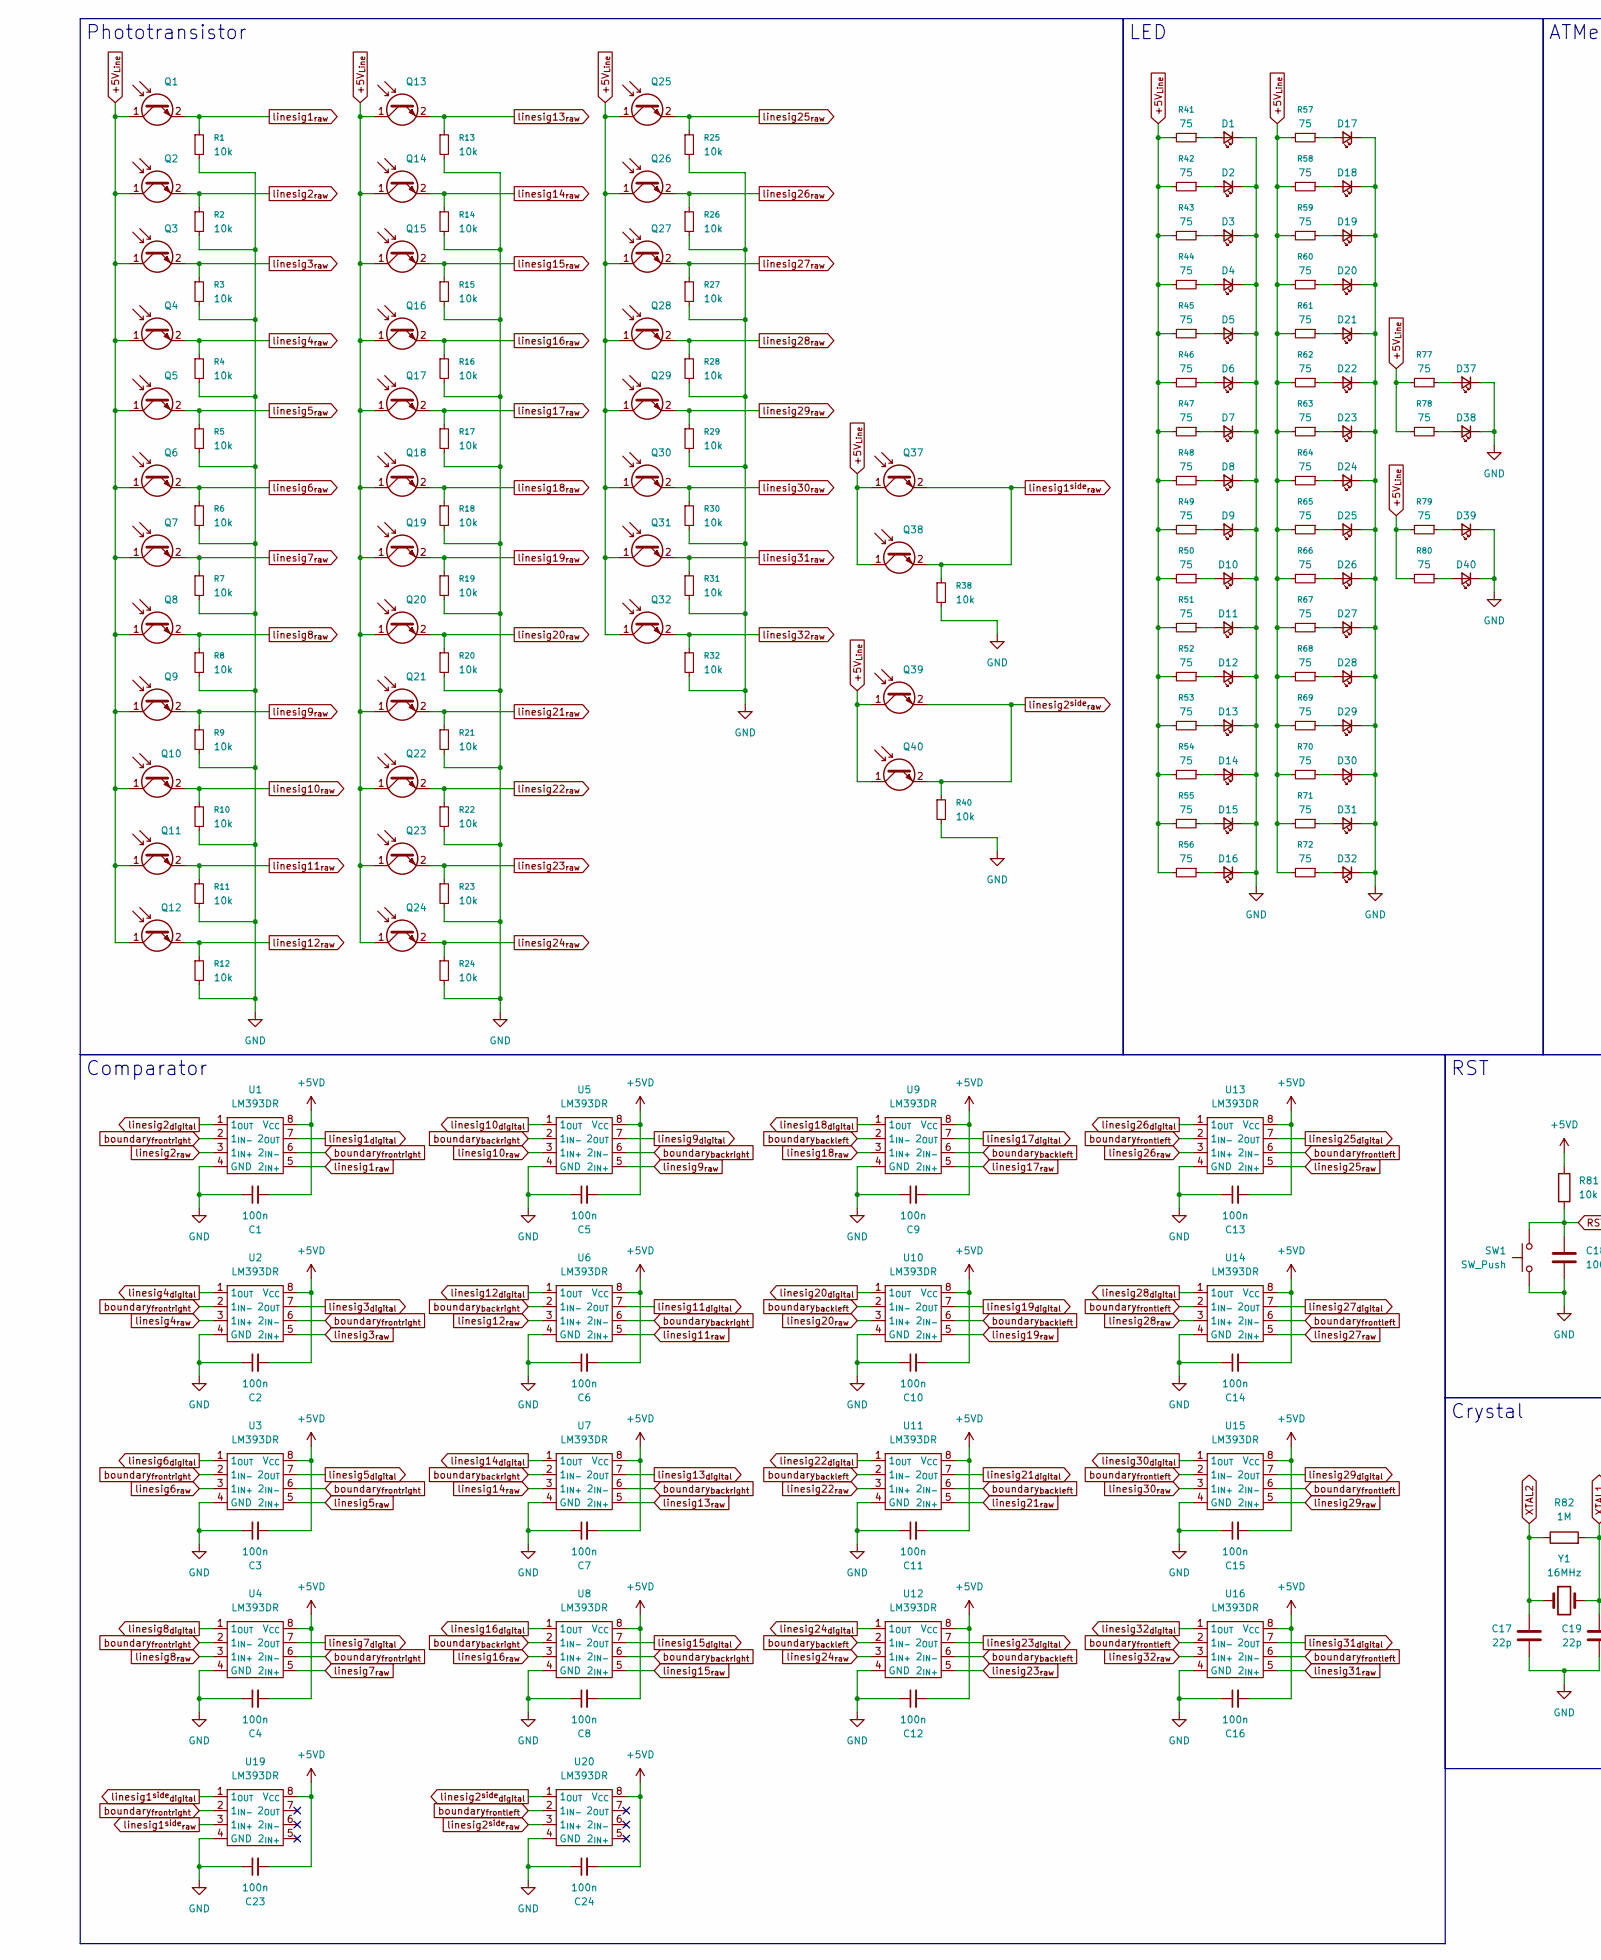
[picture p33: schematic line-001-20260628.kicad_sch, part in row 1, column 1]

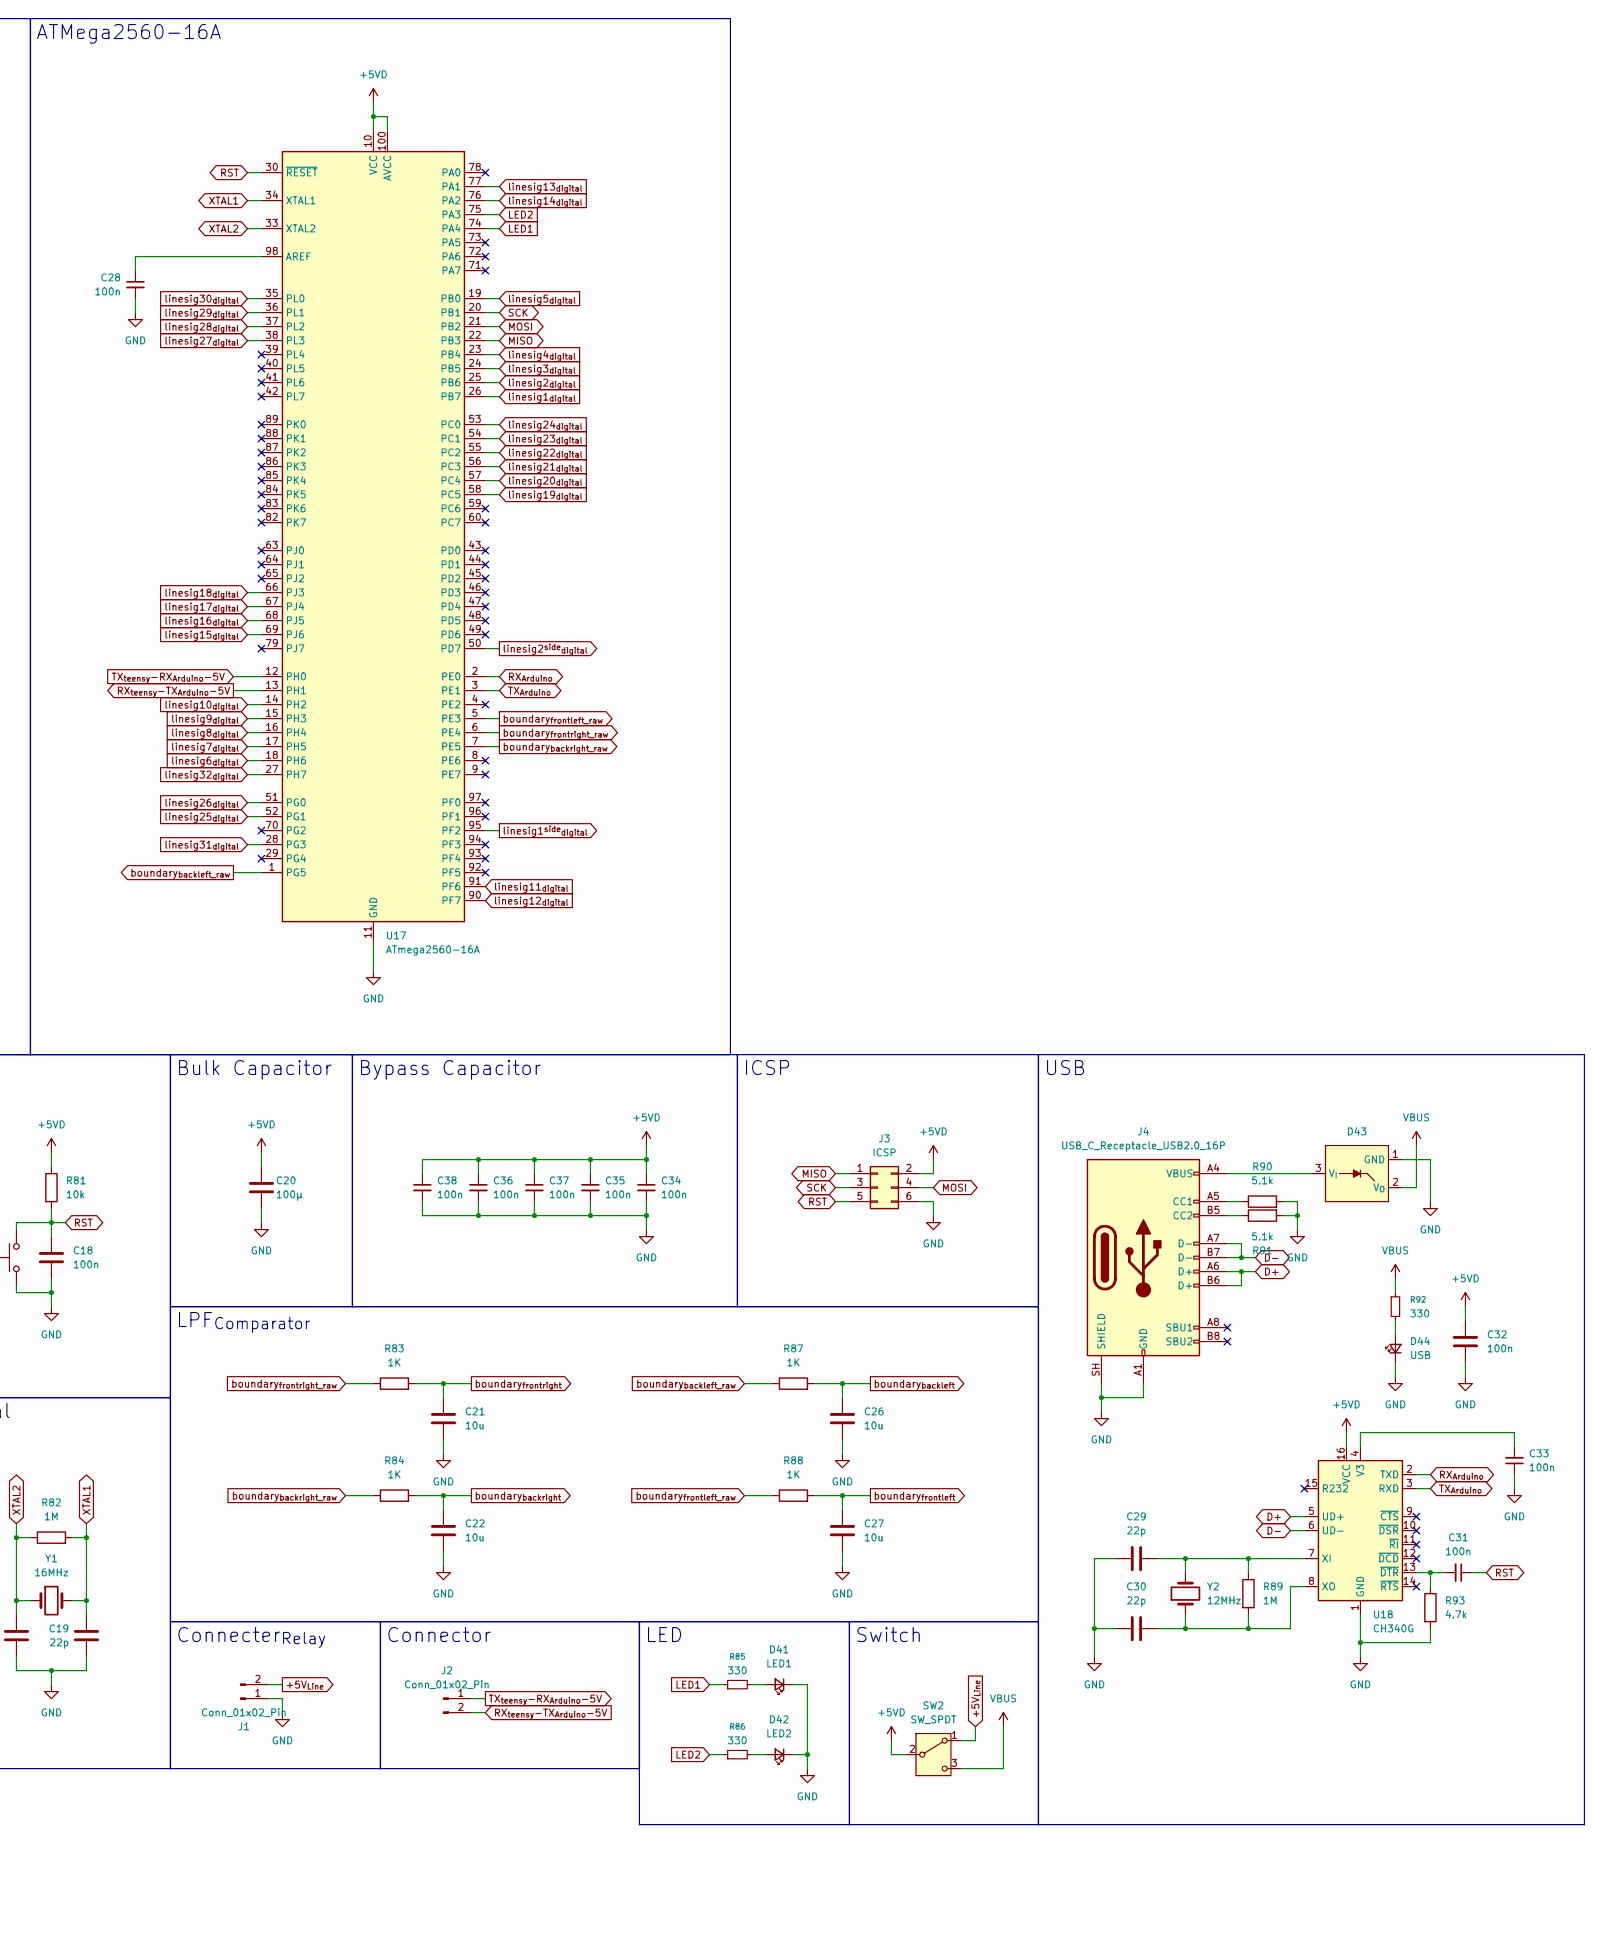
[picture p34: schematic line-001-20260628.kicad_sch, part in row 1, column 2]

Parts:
C1, C2, C3, C4, C5, C6, C7, C8, C9, C10, C11, C12, C13, C14, C15, C16, C18, C23, C24, C28, C31, C32, C33, C34, C35, C36, C37, C38: 100n; C_0805_2012Metric
C17, C19, C29, C30: 22p; C_0603_1608Metric
C20: 100μ; C_1206_3216Metric
C21, C22, C26, C27: 10u; C_0805_2012Metric
D1, D2, D3, D4, D5, D6, D7, D8, D9, D10, D11, D12, D13, D14, D15, D16, D17, D18, D19, D20, D21, D22, D23, D24, D25, D26, D27, D28, D29, D30, D31, D32, D37, D38, D39, D40: LED_Small; LED_D3.0mm
D41: LED1; LED_0603_1608Metric
D42: LED2; LED_0603_1608Metric
D43: TSOT-23
D44: USB; LED_0603_1608Metric
J1: Conn_01x02_Pin; AMASS_XT30U-M_1x02_P5.0mm_Vertical
J2: Conn_01x02_Pin; Conn_01x02_Wire_Only
J3: ICSP; PinHeader_2x03_P2.54mm_Vertical
J4: USB_C_Receptacle_USB2.0_16P; USB_C_Receptacle_HCTL_HC-TYPE-C-16P-01A
Q1, Q2, Q3, Q4, Q5, Q6, Q7, Q8, Q9, Q10, Q11, Q12, Q13, Q14, Q15, Q16, Q17, Q18, Q19, Q20, Q21, Q22, Q23, Q24, Q25, Q26, Q27, Q28, Q29, Q30, Q31, Q32, Q37, Q38, Q39, Q40: Q_Photo_NPN_CE; NJL7502L
R1, R2, R3, R4, R5, R6, R7, R8, R9, R10, R11, R12, R13, R14, R15, R16, R17, R18, R19, R20, R21, R22, R23, R24, R25, R26, R27, R28, R29, R30, R31, R32, R38, R40, R81: 10k; R_0805_2012Metric
R41, R42, R43, R44, R45, R46, R47, R48, R49, R50, R51, R52, R53, R54, R55, R56, R57, R58, R59, R60, R61, R62, R63, R64, R65, R66, R67, R68, R69, R70, R71, R72, R77, R78, R79, R80: 75; R_0805_2012Metric
R82, R89: 1M; R_0805_2012Metric
R83, R84, R87, R88: 1K; R_0805_2012Metric
R85, R86, R92: 330; R_0805_2012Metric
R90, R91: 5.1k; R_0805_2012Metric
R93: 4.7k; R_0805_2012Metric
SW1: SW_Push; TVBP06-B043C
SW2: SW_SPDT; SS12D01G4
U1, U2, U3, U4, U5, U6, U7, U8, U9, U10, U11, U12, U13, U14, U15, U16, U19, U20: LM393DR; SOIC-8_3.9x4.9mm_P1.27mm
U17: ATmega2560-16A; TQFP-100_14x14mm_P0.5mm
U18: CH340G; SOIC-16_3.9x9.9mm_P1.27mm
Y1: 16MHz; Crystal_SMD_SeikoEpson_FA238-4Pin_3.2x2.5mm
Y2: 12MHz; Crystal_SMD_SeikoEpson_FA238V-4Pin_3.2x2.5mm

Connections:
+5VD: C1.2, C2.2, C3.2, C4.2, C5.2, C6.2, C7.2, C8.2, C9.2, C10.2, C11.2, C12.2, C13.2, C14.2, C15.2, C16.2, C20.1, C23.2, C24.2, C32.2, C34.1, C35.1, C36.1, C37.1, C38.1, J3.2, R81.1, SW2.2 (B), U1.8 (V_{CC}), U2.8 (V_{CC}), U3.8 (V_{CC}), U4.8 (V_{CC}), U5.8 (V_{CC}), U6.8 (V_{CC}), U7.8 (V_{CC}), U8.8 (V_{CC}), U9.8 (V_{CC}), U10.8 (V_{CC}), U11.8 (V_{CC}), U12.8 (V_{CC}), U13.8 (V_{CC}), U14.8 (V_{CC}), U15.8 (V_{CC}), U16.8 (V_{CC}), U17.10 (VCC), U17.31 (VCC), U17.61 (VCC), U17.80 (VCC), U17.100 (AVCC), U18.16 (VCC), U19.8 (V_{CC}), U20.8 (V_{CC})
+5V_{Line}: J1.2, Q1.1 (C), Q2.1 (C), Q3.1 (C), Q4.1 (C), Q5.1 (C), Q6.1 (C), Q7.1 (C), Q8.1 (C), Q9.1 (C), Q10.1 (C), Q11.1 (C), Q12.1 (C), Q13.1 (C), Q14.1 (C), Q15.1 (C), Q16.1 (C), Q17.1 (C), Q18.1 (C), Q19.1 (C), Q20.1 (C), Q21.1 (C), Q22.1 (C), Q23.1 (C), Q24.1 (C), Q25.1 (C), Q26.1 (C), Q27.1 (C), Q28.1 (C), Q29.1 (C), Q30.1 (C), Q31.1 (C), Q32.1 (C), Q37.1 (C), Q38.1 (C), Q39.1 (C), Q40.1 (C), R41.2, R42.2, R43.2, R44.2, R45.2, R46.2, R47.2, R48.2, R49.2, R50.2, R51.2, R52.2, R53.2, R54.2, R55.2, R56.2, R57.2, R58.2, R59.2, R60.2, R61.2, R62.2, R63.2, R64.2, R65.2, R66.2, R67.2, R68.2, R69.2, R70.2, R71.2, R72.2, R77.2, R78.2, R79.2, R80.2, SW2.1 (A)
D+: J4.A6 (D+), J4.B6 (D+), U18.5 (UD+)
D-: J4.A7 (D-), J4.B7 (D-), U18.6 (UD-)
GND: C1.1, C2.1, C3.1, C4.1, C5.1, C6.1, C7.1, C8.1, C9.1, C10.1, C11.1, C12.1, C13.1, C14.1, C15.1, C16.1, C17.2, C18.2, C19.2, C20.2, C21.2, C22.2, C23.1, C24.1, C26.2, C27.2, C28.2, C29.1, C30.1, C32.1, C33.1, C34.2, C35.2, C36.2, C37.2, C38.2, D1.1 (K), D2.1 (K), D3.1 (K), D4.1 (K), D5.1 (K), D6.1 (K), D7.1 (K), D8.1 (K), D9.1 (K), D10.1 (K), D11.1 (K), D12.1 (K), D13.1 (K), D14.1 (K), D15.1 (K), D16.1 (K), D17.1 (K), D18.1 (K), D19.1 (K), D20.1 (K), D21.1 (K), D22.1 (K), D23.1 (K), D24.1 (K), D25.1 (K), D26.1 (K), D27.1 (K), D28.1 (K), D29.1 (K), D30.1 (K), D31.1 (K), D32.1 (K), D37.1 (K), D38.1 (K), D39.1 (K), D40.1 (K), D41.1 (K), D42.1 (K), D43.1 (GND), D44.1 (K), J1.1, J3.6, J4.A1 (GND), J4.A12 (GND), J4.B1 (GND), J4.B12 (GND), J4.SH (SHIELD), R1.2, R2.2, R3.2, R4.2, R5.2, R6.2, R7.2, R8.2, R9.2, R10.2, R11.2, R12.2, R13.2, R14.2, R15.2, R16.2, R17.2, R18.2, R19.2, R20.2, R21.2, R22.2, R23.2, R24.2, R25.2, R26.2, R27.2, R28.2, R29.2, R30.2, R31.2, R32.2, R38.2, R40.2, R90.2, R91.2, R93.2, SW1.1, U1.4 (GND), U2.4 (GND), U3.4 (GND), U4.4 (GND), U5.4 (GND), U6.4 (GND), U7.4 (GND), U8.4 (GND), U9.4 (GND), U10.4 (GND), U11.4 (GND), U12.4 (GND), U13.4 (GND), U14.4 (GND), U15.4 (GND), U16.4 (GND), U17.11 (GND), U17.32 (GND), U17.62 (GND), U17.81 (GND), U17.99 (GND), U18.1 (GND), U19.4 (GND), U20.4 (GND)
LED1: R85.1, U17.74 (PA4)
LED2: R86.1, U17.75 (PA3)
MISO: J3.1, U17.22 (PB3)
MOSI: J3.4, U17.21 (PB2)
unnamed: D1.2 (A), R41.1
unnamed: D2.2 (A), R42.1
unnamed: D3.2 (A), R43.1
unnamed: D4.2 (A), R44.1
unnamed: D5.2 (A), R45.1
unnamed: D6.2 (A), R46.1
unnamed: D7.2 (A), R47.1
unnamed: D8.2 (A), R48.1
unnamed: D9.2 (A), R49.1
unnamed: D10.2 (A), R50.1
unnamed: D11.2 (A), R51.1
unnamed: D12.2 (A), R52.1
unnamed: D13.2 (A), R53.1
unnamed: D14.2 (A), R54.1
unnamed: D15.2 (A), R55.1
unnamed: D16.2 (A), R56.1
unnamed: D17.2 (A), R57.1
unnamed: D18.2 (A), R58.1
unnamed: D19.2 (A), R59.1
unnamed: D20.2 (A), R60.1
unnamed: D21.2 (A), R61.1
unnamed: D22.2 (A), R62.1
unnamed: D23.2 (A), R63.1
unnamed: D24.2 (A), R64.1
unnamed: D25.2 (A), R65.1
unnamed: D26.2 (A), R66.1
unnamed: D27.2 (A), R67.1
unnamed: D28.2 (A), R68.1
unnamed: D29.2 (A), R69.1
unnamed: D30.2 (A), R70.1
unnamed: D31.2 (A), R71.1
unnamed: D32.2 (A), R72.1
unnamed: D37.2 (A), R77.1
unnamed: D38.2 (A), R78.1
unnamed: D39.2 (A), R79.1
unnamed: D40.2 (A), R80.1
unnamed: D41.2 (A), R85.2
unnamed: D42.2 (A), R86.2
unnamed: D43.3 (V_{I}), J4.A4 (VBUS), J4.A9 (VBUS), J4.B4 (VBUS), J4.B9 (VBUS)
unnamed: D44.2 (A), R92.2
unnamed: J4.A5 (CC1), R90.1
unnamed: J4.B5 (CC2), R91.1
unnamed: C28.1, U17.98 (AREF)
unnamed: C33.2, U18.4 (V3)
unnamed: C29.2, R89.1, U18.7 (XI), Y2.3
unnamed: C30.2, R89.2, U18.8 (XO), Y2.1
unnamed: C31.2, R93.1, U18.13 (~DTR)
RST: C18.1, C31.1, J3.5, R81.2, SW1.2, U17.30 (~RESET)
RX_{Arduino}: U17.2 (PE0), U18.2 (TXD)
RX_{teensy}-TX_{Arduino}-5V: J2.2, U17.13 (PH1)
SCK: J3.3, U17.20 (PB1)
TX_{Arduino}: U17.3 (PE1), U18.3 (RXD)
TX_{teensy}-RX_{Arduino}-5V: J2.1, U17.12 (PH0)
VBUS: D43.2 (V_{O}), R92.1, SW2.3 (C)
XTAL1: C19.1, R82.2, U17.34 (XTAL1), Y1.3
XTAL2: C17.1, R82.1, U17.33 (XTAL2), Y1.1
boundary_{backleft_raw}: R87.1, U17.1 (PG5)
boundary_{backleft}: C26.1, R87.2, U9.2 (1_{IN-}), U9.6 (2_{IN-}), U10.2 (1_{IN-}), U10.6 (2_{IN-}), U11.2 (1_{IN-}), U11.6 (2_{IN-}), U12.2 (1_{IN-}), U12.6 (2_{IN-})
boundary_{backright_raw}: R84.1, U17.7 (PE5)
boundary_{backright}: C22.1, R84.2, U5.2 (1_{IN-}), U5.6 (2_{IN-}), U6.2 (1_{IN-}), U6.6 (2_{IN-}), U7.2 (1_{IN-}), U7.6 (2_{IN-}), U8.2 (1_{IN-}), U8.6 (2_{IN-})
boundary_{frontleft_raw}: R88.1, U17.5 (PE3)
boundary_{frontleft}: C27.1, R88.2, U13.2 (1_{IN-}), U13.6 (2_{IN-}), U14.2 (1_{IN-}), U14.6 (2_{IN-}), U15.2 (1_{IN-}), U15.6 (2_{IN-}), U16.2 (1_{IN-}), U16.6 (2_{IN-}), U20.2 (1_{IN-})
boundary_{frontright_raw}: R83.1, U17.6 (PE4)
boundary_{frontright}: C21.1, R83.2, U1.2 (1_{IN-}), U1.6 (2_{IN-}), U2.2 (1_{IN-}), U2.6 (2_{IN-}), U3.2 (1_{IN-}), U3.6 (2_{IN-}), U4.2 (1_{IN-}), U4.6 (2_{IN-}), U19.2 (1_{IN-})
linesig1^{side}_{digital}: U17.95 (PF2), U19.1 (1_{OUT})
linesig1^{side}_{raw}: Q37.2 (E), Q38.2 (E), R38.1, U19.3 (1_{IN+})
linesig1_{digital}: U1.7 (2_{OUT}), U17.26 (PB7)
linesig1_{raw}: Q1.2 (E), R1.1, U1.5 (2_{IN+})
linesig2^{side}_{digital}: U17.50 (PD7), U20.1 (1_{OUT})
linesig2^{side}_{raw}: Q39.2 (E), Q40.2 (E), R40.1, U20.3 (1_{IN+})
linesig2_{digital}: U1.1 (1_{OUT}), U17.25 (PB6)
linesig2_{raw}: Q2.2 (E), R2.1, U1.3 (1_{IN+})
linesig3_{digital}: U2.7 (2_{OUT}), U17.24 (PB5)
linesig3_{raw}: Q3.2 (E), R3.1, U2.5 (2_{IN+})
linesig4_{digital}: U2.1 (1_{OUT}), U17.23 (PB4)
linesig4_{raw}: Q4.2 (E), R4.1, U2.3 (1_{IN+})
linesig5_{digital}: U3.7 (2_{OUT}), U17.19 (PB0)
linesig5_{raw}: Q5.2 (E), R5.1, U3.5 (2_{IN+})
linesig6_{digital}: U3.1 (1_{OUT}), U17.18 (PH6)
linesig6_{raw}: Q6.2 (E), R6.1, U3.3 (1_{IN+})
linesig7_{digital}: U4.7 (2_{OUT}), U17.17 (PH5)
linesig7_{raw}: Q7.2 (E), R7.1, U4.5 (2_{IN+})
linesig8_{digital}: U4.1 (1_{OUT}), U17.16 (PH4)
linesig8_{raw}: Q8.2 (E), R8.1, U4.3 (1_{IN+})
linesig9_{digital}: U5.7 (2_{OUT}), U17.15 (PH3)
linesig9_{raw}: Q9.2 (E), R9.1, U5.5 (2_{IN+})
linesig10_{digital}: U5.1 (1_{OUT}), U17.14 (PH2)
linesig10_{raw}: Q10.2 (E), R10.1, U5.3 (1_{IN+})
linesig11_{digital}: U6.7 (2_{OUT}), U17.91 (PF6)
linesig11_{raw}: Q11.2 (E), R11.1, U6.5 (2_{IN+})
linesig12_{digital}: U6.1 (1_{OUT}), U17.90 (PF7)
linesig12_{raw}: Q12.2 (E), R12.1, U6.3 (1_{IN+})
linesig13_{digital}: U7.7 (2_{OUT}), U17.77 (PA1)
linesig13_{raw}: Q13.2 (E), R13.1, U7.5 (2_{IN+})
linesig14_{digital}: U7.1 (1_{OUT}), U17.76 (PA2)
linesig14_{raw}: Q14.2 (E), R14.1, U7.3 (1_{IN+})
linesig15_{digital}: U8.7 (2_{OUT}), U17.69 (PJ6)
linesig15_{raw}: Q15.2 (E), R15.1, U8.5 (2_{IN+})
linesig16_{digital}: U8.1 (1_{OUT}), U17.68 (PJ5)
linesig16_{raw}: Q16.2 (E), R16.1, U8.3 (1_{IN+})
linesig17_{digital}: U9.7 (2_{OUT}), U17.67 (PJ4)
linesig17_{raw}: Q17.2 (E), R17.1, U9.5 (2_{IN+})
linesig18_{digital}: U9.1 (1_{OUT}), U17.66 (PJ3)
linesig18_{raw}: Q18.2 (E), R18.1, U9.3 (1_{IN+})
linesig19_{digital}: U10.7 (2_{OUT}), U17.58 (PC5)
linesig19_{raw}: Q19.2 (E), R19.1, U10.5 (2_{IN+})
linesig20_{digital}: U10.1 (1_{OUT}), U17.57 (PC4)
linesig20_{raw}: Q20.2 (E), R20.1, U10.3 (1_{IN+})
linesig21_{digital}: U11.7 (2_{OUT}), U17.56 (PC3)
linesig21_{raw}: Q21.2 (E), R21.1, U11.5 (2_{IN+})
linesig22_{digital}: U11.1 (1_{OUT}), U17.55 (PC2)
linesig22_{raw}: Q22.2 (E), R22.1, U11.3 (1_{IN+})
linesig23_{digital}: U12.7 (2_{OUT}), U17.54 (PC1)
linesig23_{raw}: Q23.2 (E), R23.1, U12.5 (2_{IN+})
linesig24_{digital}: U12.1 (1_{OUT}), U17.53 (PC0)
linesig24_{raw}: Q24.2 (E), R24.1, U12.3 (1_{IN+})
linesig25_{digital}: U13.7 (2_{OUT}), U17.52 (PG1)
linesig25_{raw}: Q25.2 (E), R25.1, U13.5 (2_{IN+})
linesig26_{digital}: U13.1 (1_{OUT}), U17.51 (PG0)
linesig26_{raw}: Q26.2 (E), R26.1, U13.3 (1_{IN+})
linesig27_{digital}: U14.7 (2_{OUT}), U17.38 (PL3)
linesig27_{raw}: Q27.2 (E), R27.1, U14.5 (2_{IN+})
linesig28_{digital}: U14.1 (1_{OUT}), U17.37 (PL2)
linesig28_{raw}: Q28.2 (E), R28.1, U14.3 (1_{IN+})
linesig29_{digital}: U15.7 (2_{OUT}), U17.36 (PL1)
linesig29_{raw}: Q29.2 (E), R29.1, U15.5 (2_{IN+})
linesig30_{digital}: U15.1 (1_{OUT}), U17.35 (PL0)
linesig30_{raw}: Q30.2 (E), R30.1, U15.3 (1_{IN+})
linesig31_{digital}: U16.7 (2_{OUT}), U17.28 (PG3)
linesig31_{raw}: Q31.2 (E), R31.1, U16.5 (2_{IN+})
linesig32_{digital}: U16.1 (1_{OUT}), U17.27 (PH7)
linesig32_{raw}: Q32.2 (E), R32.1, U16.3 (1_{IN+})

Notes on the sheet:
Phototransistor
Bypass Capacitor
LED
Switch
Bulk Capacitor
Connecter_{Relay}
ATMega2560-16A
LPF_{Comparator}
Comparator
RST
ICSP
Connector
USB
Crystal

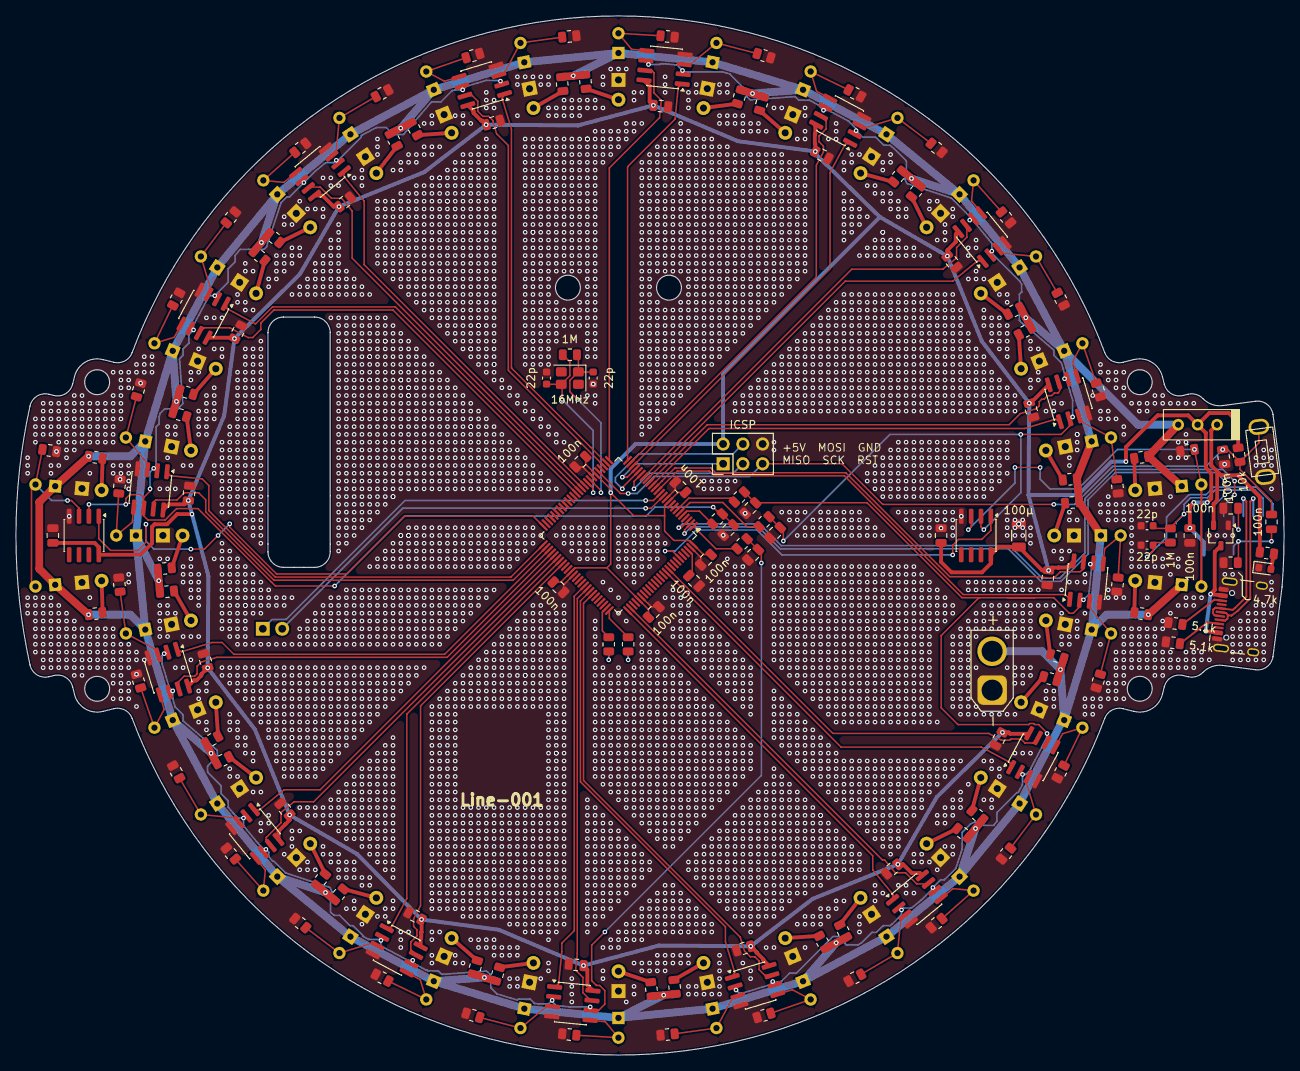
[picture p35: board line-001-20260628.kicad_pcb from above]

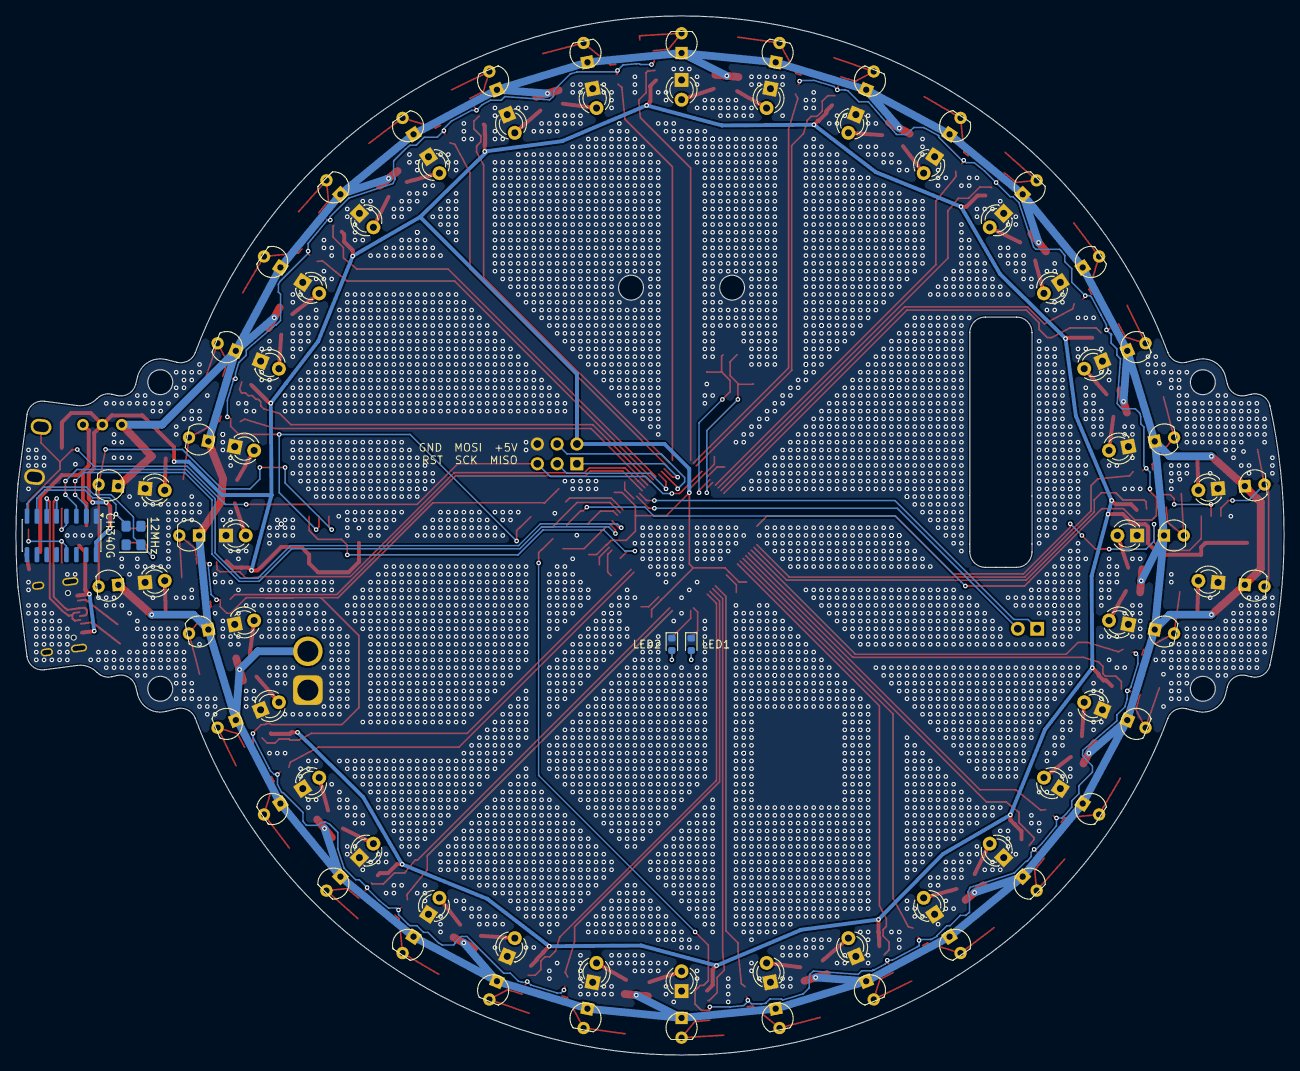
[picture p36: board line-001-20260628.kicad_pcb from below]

Board: 2 copper layers, 163.1 x 133.7 mm, 224 parts (76 on the bottom side), 141 nets.

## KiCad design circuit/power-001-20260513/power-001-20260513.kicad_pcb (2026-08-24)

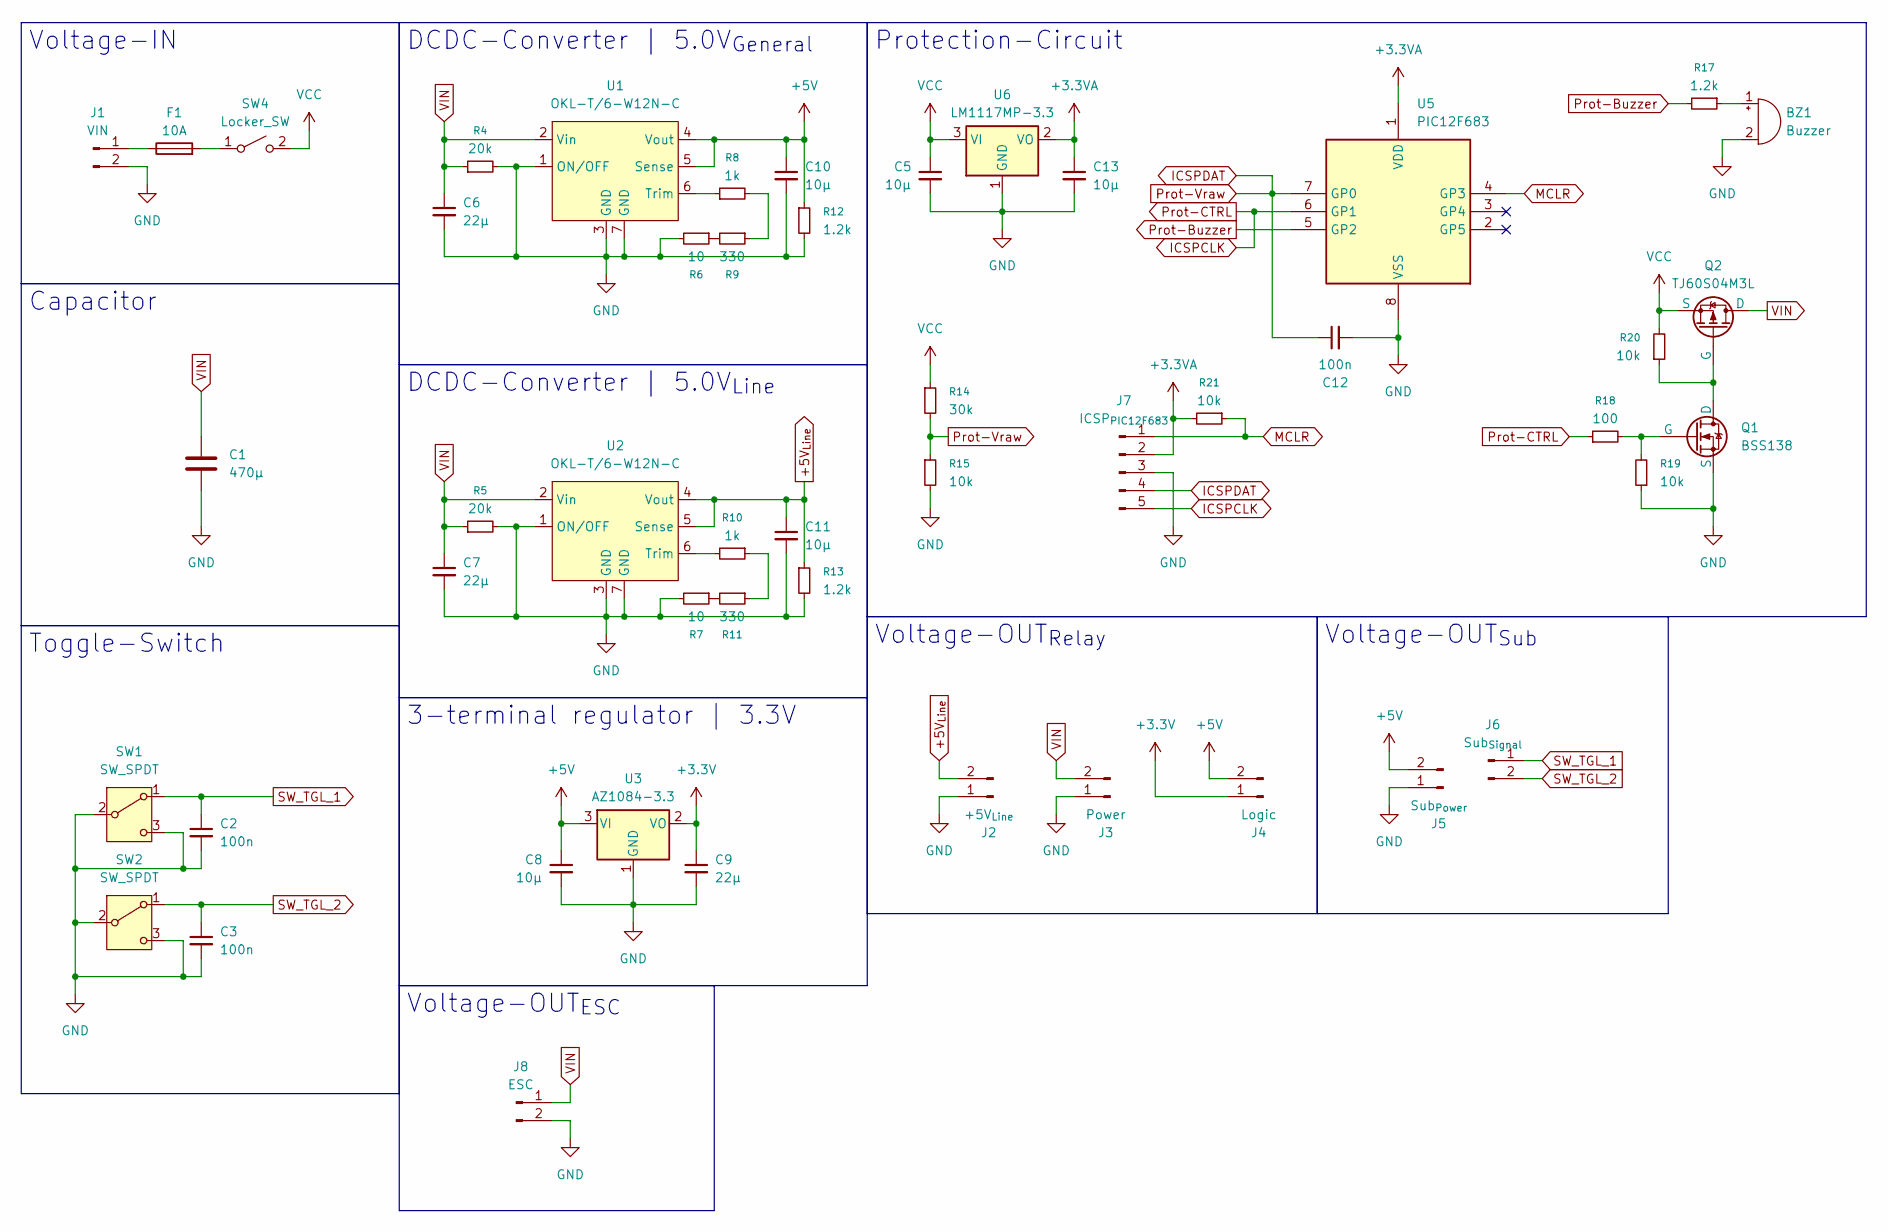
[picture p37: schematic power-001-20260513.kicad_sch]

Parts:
BZ1: Buzzer; PKM13EPYH4000-A0
C1: 470μ; CP_Radial_D8.0mm_P3.50mm
C2, C3, C12: 100n; C_0805_2012Metric
C5, C8, C10, C11, C13: 10μ; C_0805_2012Metric
C6, C7, C9: 22μ; C_0805_2012Metric
F1: 10A; MF61NR_FUC-04
J1: VIN; Conn_01x02_Wire_Only
J2: +5V_{Line}; AMASS_XT30PW-F_1x02_P2.50mm_Horizontal
J3: Power; AMASS_XT30PW-F_1x02_P2.50mm_Horizontal
J4: Logic; AMASS_XT30PW-F_1x02_P2.50mm_Horizontal
J5: Sub_{Power}; AMASS_XT30PW-F_1x02_P2.50mm_Horizontal
J6: Sub_{Signal}; PinHeader_1x02_P2.54mm_Horizontal
J7: ICSP_{PIC12F683}; PinHeader_1x05_P1.00mm_Vertical
J8: ESC; Conn_01x02_Wire_Only_SMD
Q1: BSS138; TSOT-23
Q2: TJ60S04M3L; TO-252-2
R4, R5: 20k; R_0805_2012Metric
R6, R7: 10; R_0805_2012Metric
R8, R10: 1k; R_0805_2012Metric
R9, R11: 330; R_0805_2012Metric
R12, R13, R17: 1.2k; R_0805_2012Metric
R14: 30k; R_0805_2012Metric
R15, R19, R20, R21: 10k; R_0805_2012Metric
R18: 100; R_0805_2012Metric
SW1, SW2: SW_SPDT; 2MS1-T1-B4-M2-Q-E
SW4: Locker_SW; DS-850K-S-ON-K
U1, U2: OKL-T/6-W12N-C; OKL-T6-W12N-C
U3: AZ1084-3.3; TO-252-2
U5: PIC12F683; SOIC-8_3.9x4.9mm_P1.27mm
U6: LM1117MP-3.3; SOT-223-3_TabPin2

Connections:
+3.3V: C9.1, J4.1, U3.2 (VO)
+3.3VA: C13.1, J7.2, R21.2, U5.1 (VDD), U6.2 (VO)
+5V: C8.1, C10.1, J4.2, J5.2, R12.1, U1.4 (Vout), U1.5 (Sense), U3.3 (VI)
+5V_{Line}: C11.1, J2.2, R13.1, U2.4 (Vout), U2.5 (Sense)
GND: BZ1.2 (-), C1.2, C2.2, C3.2, C5.2, C6.2, C7.2, C8.2, C9.2, C10.2, C11.2, C12.2, C13.2, J1.2, J2.1, J3.1, J5.1, J7.3, J8.2, Q1.3 (S), R4.2, R5.2, R6.2, R7.2, R12.2, R13.2, R15.2, R19.1, SW1.2 (B), SW1.3 (C), SW2.2 (B), SW2.3 (C), U1.1 (ON/OFF), U1.3 (GND), U1.7 (GND), U2.1 (ON/OFF), U2.3 (GND), U2.7 (GND), U3.1 (GND), U5.8 (VSS), U6.1 (GND)
ICSPCLK: J7.5, R18.1, U5.6 (GP1)
ICSPDAT: C12.1, J7.4, R14.2, R15.1, U5.7 (GP0)
MCLR: J7.1, R21.1, U5.4 (GP3)
unnamed: BZ1.1 (+), R17.1
unnamed: F1.1, J1.1
unnamed: Q1.1 (D), Q2.1 (G), R20.1
unnamed: Q1.2 (G), R18.2, R19.2
unnamed: R6.1, R9.2
unnamed: R8.2, R9.1
unnamed: R10.1, R11.1
unnamed: R7.1, R11.2
unnamed: F1.2, SW4.1 (A)
unnamed: R8.1, U1.6 (Trim)
unnamed: R10.2, U2.6 (Trim)
Prot-Buzzer: R17.2, U5.5 (GP2)
SW_TGL_1: C2.1, J6.1, SW1.1 (A)
SW_TGL_2: C3.1, J6.2, SW2.1 (A)
VCC: C5.1, Q2.3 (S), R14.1, R20.2, SW4.2 (B), U6.3 (VI)
VIN: C1.1, C6.1, C7.1, J3.2, J8.1, Q2.2 (D), R4.1, R5.1, U1.2 (Vin), U2.2 (Vin)

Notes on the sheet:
DCDC-Converter | 5.0V_{General}
Voltage-OUT_{ESC}
Protection-Circuit
Toggle-Switch
Voltage-OUT_{Sub}
Capacitor
DCDC-Converter | 5.0V_{Line}
3-terminal regulator | 3.3V
Voltage-OUT_{Relay}
Voltage-IN

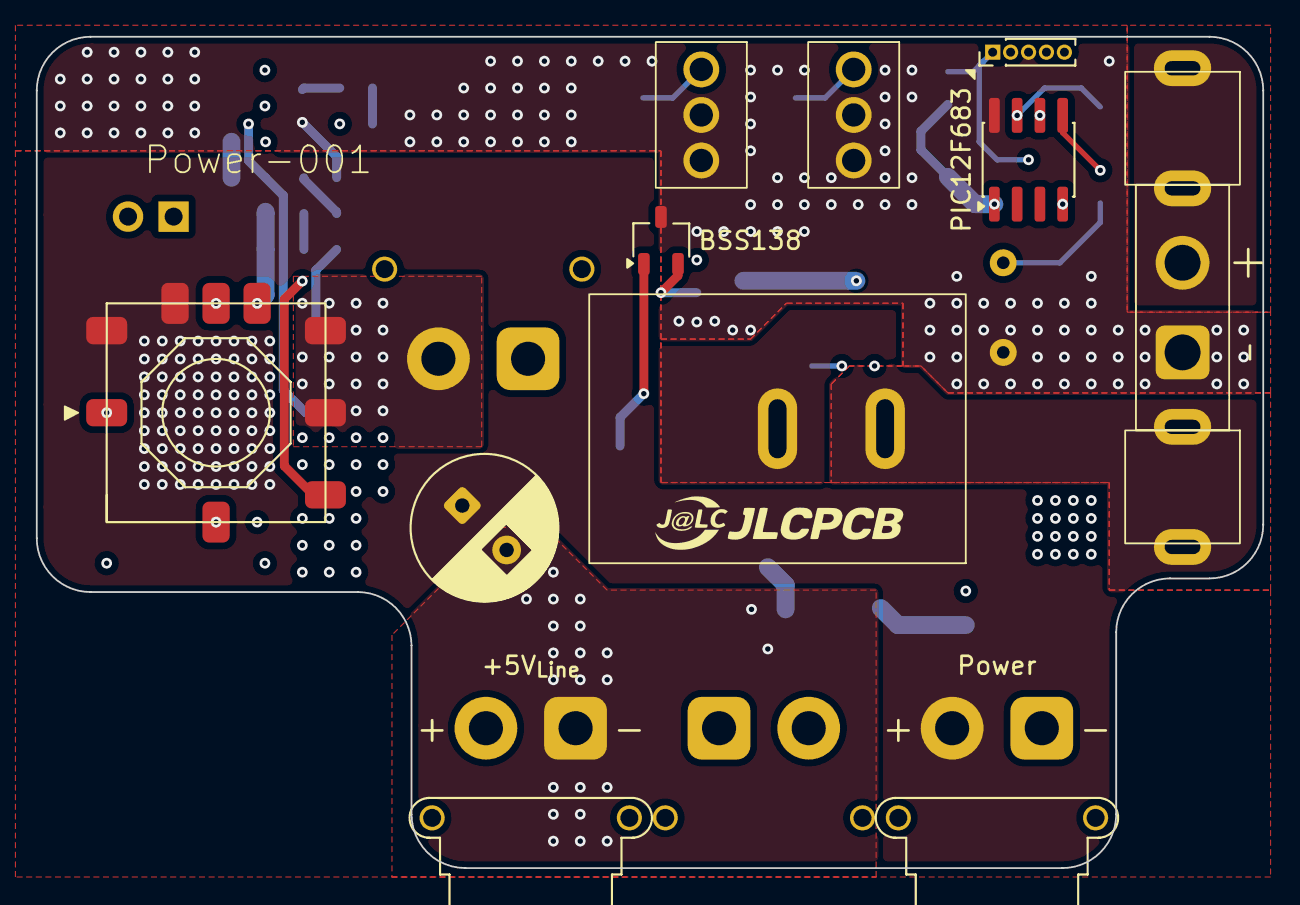
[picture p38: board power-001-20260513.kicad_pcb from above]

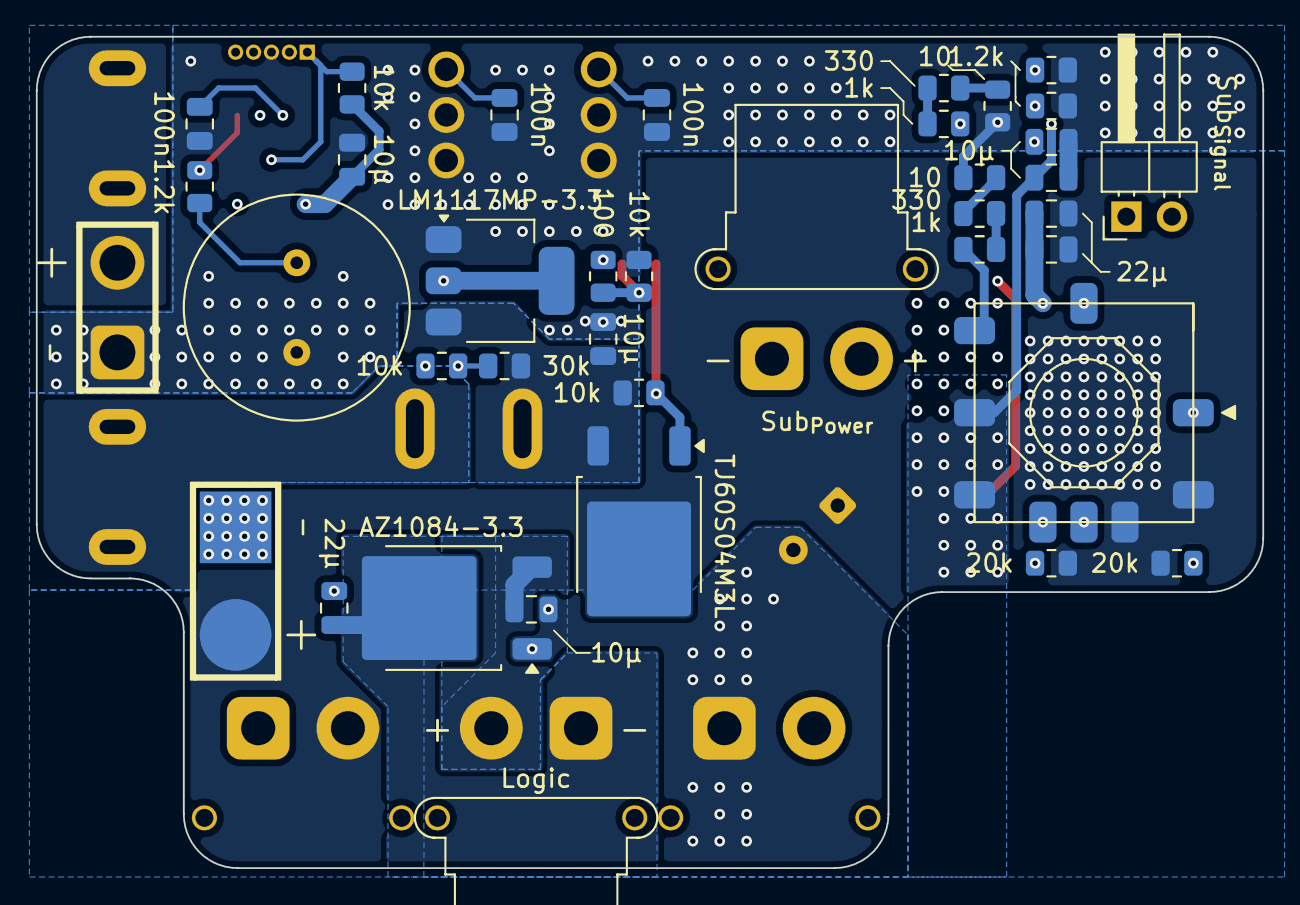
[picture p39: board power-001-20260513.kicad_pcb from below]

Board: 4 copper layers, 68.4 x 46.4 mm, 49 parts (38 on the bottom side), 24 nets.

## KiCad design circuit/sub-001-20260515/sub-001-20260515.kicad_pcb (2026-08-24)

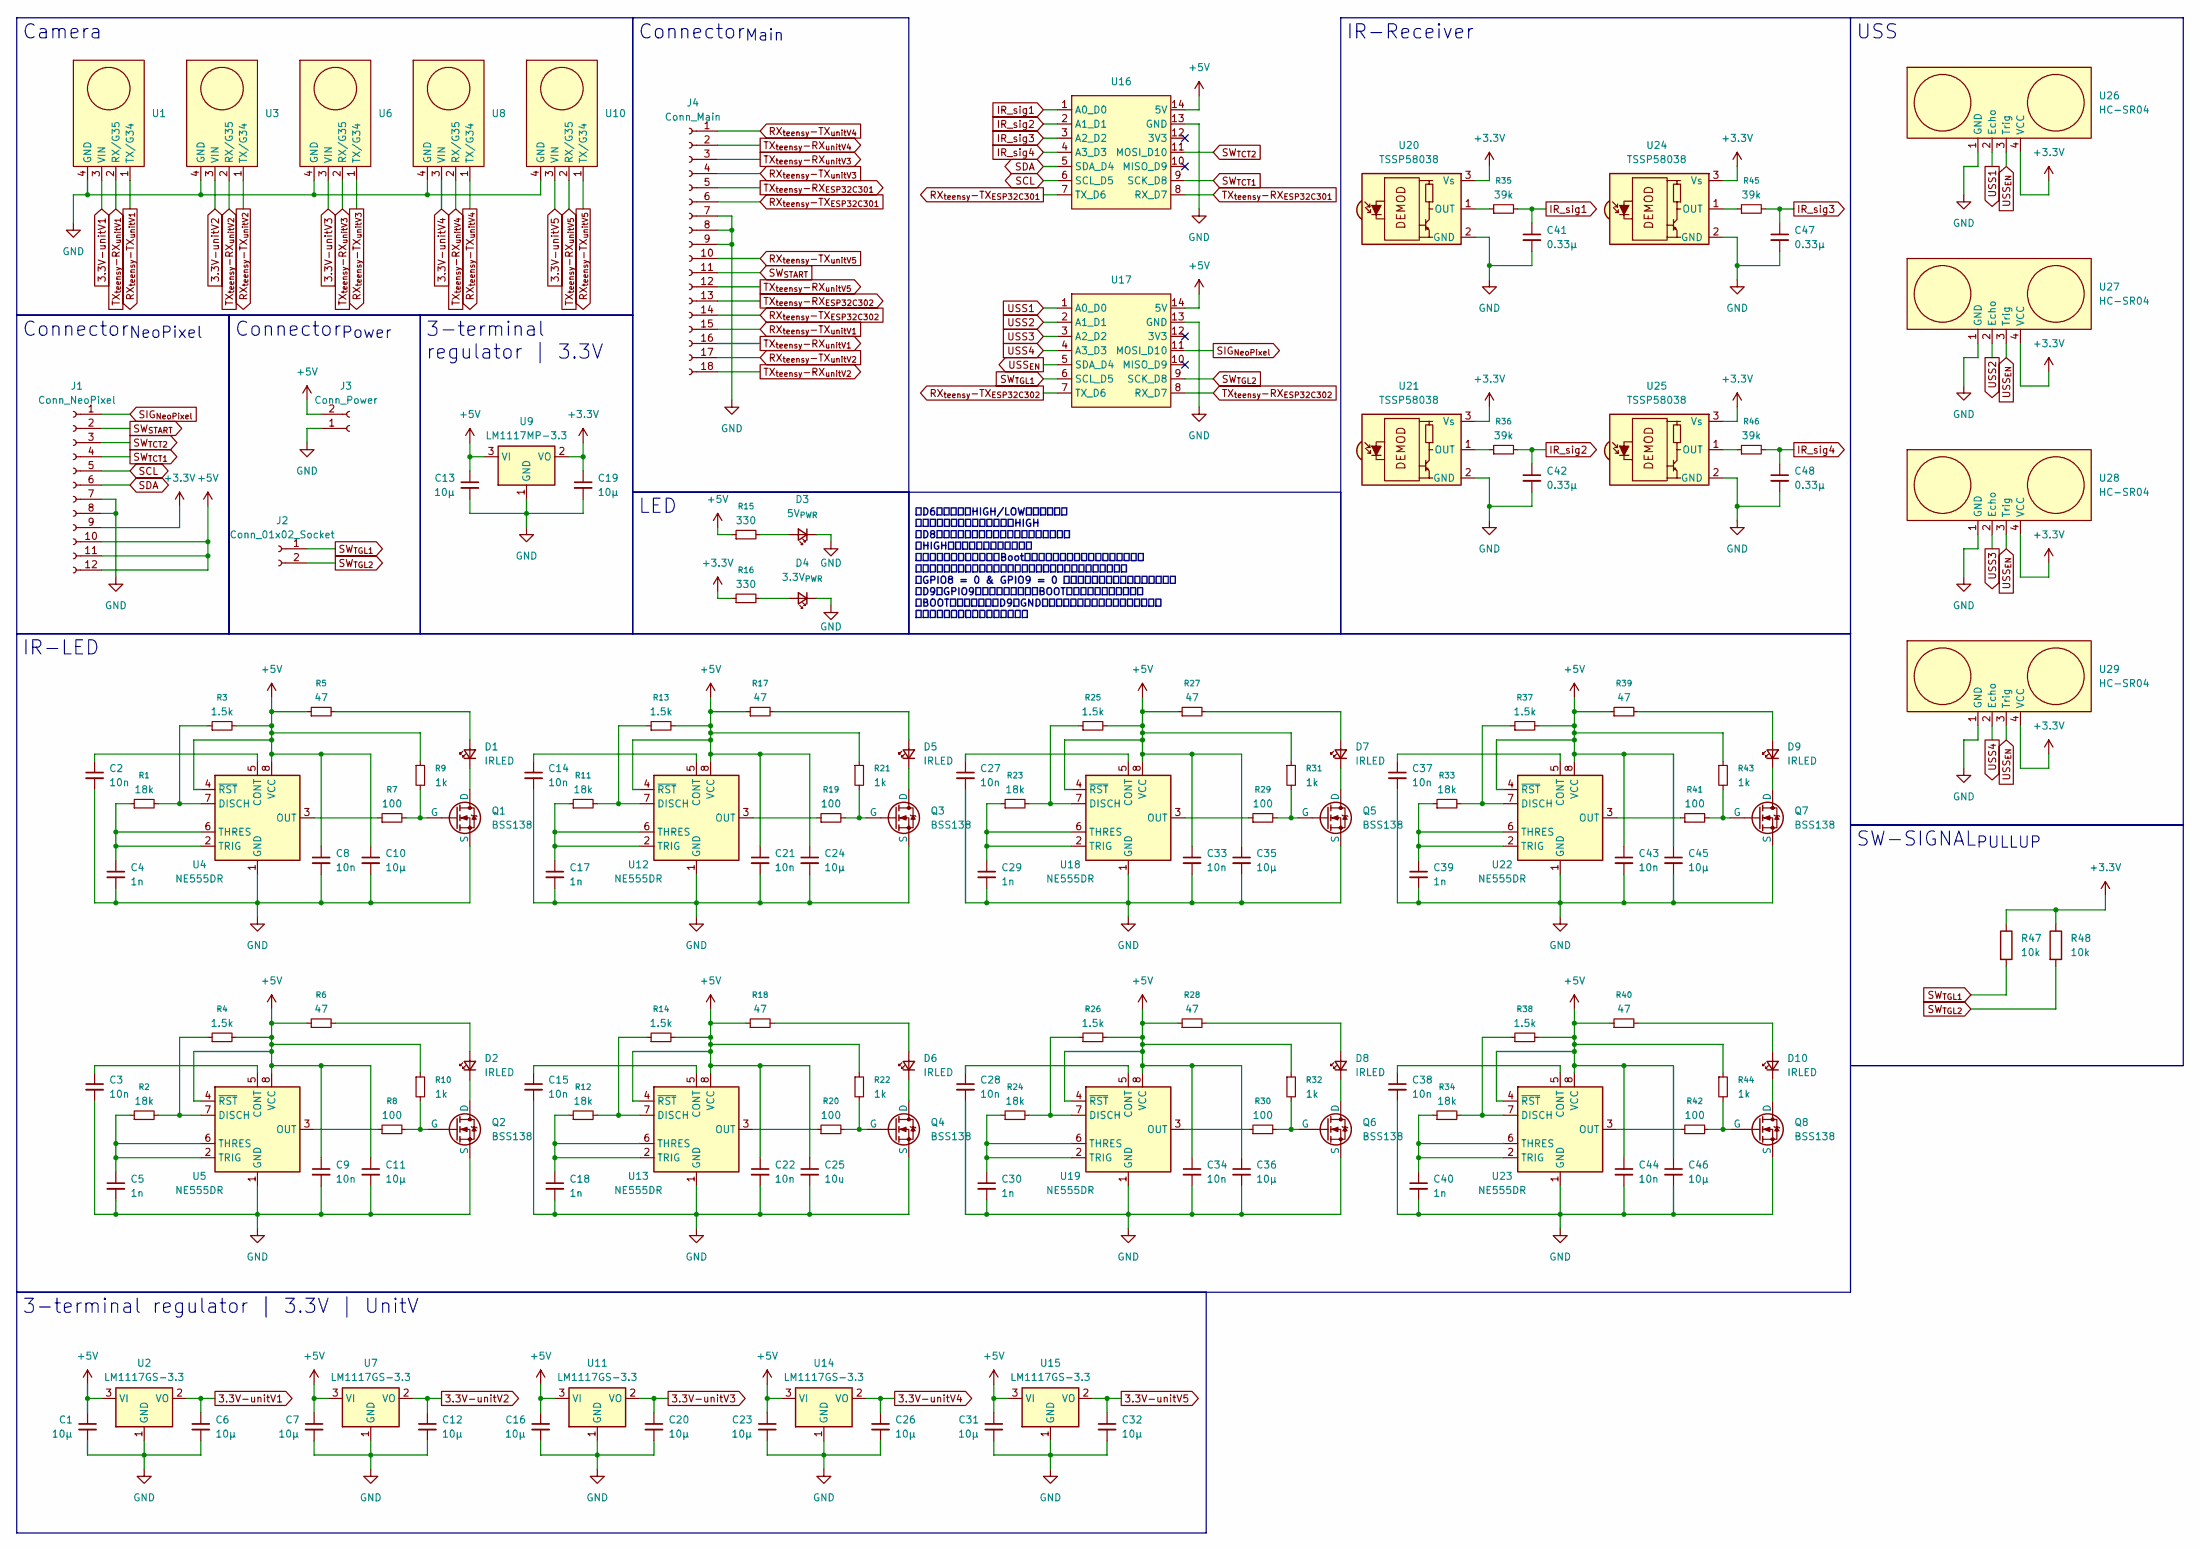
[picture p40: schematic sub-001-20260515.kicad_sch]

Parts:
C1, C6, C7, C10, C11, C12, C13, C16, C19, C20, C23, C24, C26, C31, C32, C35, C36, C45, C46: 10μ; C_0805_2012Metric
C2, C3, C8, C9, C14, C15, C21, C22, C27, C28, C33, C34, C37, C38, C43, C44: 10n; C_0805_2012Metric
C4, C5, C17, C18, C29, C30, C39, C40: 1n; C_0805_2012Metric
C25: 10u; C_0805_2012Metric
C41, C42, C47, C48: 0.33μ; C_0805_2012Metric
D1, D2, D5, D6, D7, D8, D9, D10: IRLED; LED_D3.0mm
D3: 5V_{PWR}; LED_0603_1608Metric
D4: 3.3V_{PWR}; LED_0603_1608Metric
J1: Conn_NeoPixel; AFC01-S12FCA-00
J2: Conn_01x02_Socket; PinSocket_1x02_P2.54mm_Vertical
J3: Conn_Power; AMASS_XT30U-M_1x02_P5.0mm_Vertical
J4: Conn_Main; AFC01-S18FCA-00
Q1, Q2, Q3, Q4, Q5, Q6, Q7, Q8: BSS138; SOT-23
R1, R2, R11, R12, R23, R24, R33, R34: 18k; R_0805_2012Metric
R3, R4, R13, R14, R25, R26, R37, R38: 1.5k; R_0805_2012Metric
R5, R6, R17, R18, R27, R28, R39, R40: 47; R_0805_2012Metric
R7, R8, R19, R20, R29, R30, R41, R42: 100; R_0805_2012Metric
R9, R10, R21, R22, R31, R32, R43, R44: 1k; R_0805_2012Metric
R15, R16: 330; R_0805_2012Metric
R35, R36, R45, R46: 39k; R_0805_2012Metric
R47, R48: 10k; R_0805_2012Metric
U1, U3, U6, U8, U10: NS-Tech_Grove_1x04_P2mm_Vertical
U2, U7, U11, U14, U15: LM1117GS-3.3; SOT-223-3_TabPin2
U4, U5, U12, U13, U18, U19, U22, U23: NE555DR; SOIC-8_3.9x4.9mm_P1.27mm
U9: LM1117MP-3.3; SOT-223-3_TabPin2
U16, U17: XIAO-ESP32-C3-DIP
U20, U21, U24, U25: TSSP58038; Vishay_MINICAST-3Pin
U26, U27, U28, U29: HC-SR04; PinHeader_1x04_P2.54mm_Vertical

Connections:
3.3V-unitV1: C6.1, U1.3 (VIN), U2.2 (VO)
3.3V-unitV2: C12.1, U3.3 (VIN), U7.2 (VO)
3.3V-unitV3: C20.1, U6.3 (VIN), U11.2 (VO)
3.3V-unitV4: C26.1, U8.3 (VIN), U14.2 (VO)
3.3V-unitV5: C32.1, U10.3 (VIN), U15.2 (VO)
+3.3V: C19.1, J1.9, R16.1, R47.1, R48.1, U9.2 (VO), U20.3 (Vs), U21.3 (Vs), U24.3 (Vs), U25.3 (Vs), U26.4 (VCC), U27.4 (VCC), U28.4 (VCC), U29.4 (VCC)
+5V: C1.1, C7.1, C8.1, C9.1, C10.1, C11.1, C13.1, C16.1, C21.1, C22.1, C23.1, C24.1, C25.1, C31.1, C33.1, C34.1, C35.1, C36.1, C43.1, C44.1, C45.1, C46.1, J1.10, J1.11, J1.12, J3.2, R3.2, R4.2, R5.1, R6.1, R9.1, R10.1, R13.2, R14.2, R15.1, R17.1, R18.1, R21.1, R22.1, R25.2, R26.2, R27.1, R28.1, R31.1, R32.1, R37.2, R38.2, R39.1, R40.1, R43.1, R44.1, U2.3 (VI), U4.4 (~RST), U4.8 (VCC), U5.4 (~RST), U5.8 (VCC), U7.3 (VI), U9.3 (VI), U11.3 (VI), U12.4 (~RST), U12.8 (VCC), U13.4 (~RST), U13.8 (VCC), U14.3 (VI), U15.3 (VI), U16.14 (5V), U17.14 (5V), U18.4 (~RST), U18.8 (VCC), U19.4 (~RST), U19.8 (VCC), U22.4 (~RST), U22.8 (VCC), U23.4 (~RST), U23.8 (VCC)
GND: C1.2, C2.2, C3.2, C4.2, C5.2, C6.2, C7.2, C8.2, C9.2, C10.2, C11.2, C12.2, C13.2, C14.2, C15.2, C16.2, C17.2, C18.2, C19.2, C20.2, C21.2, C22.2, C23.2, C24.2, C25.2, C26.2, C27.2, C28.2, C29.2, C30.2, C31.2, C32.2, C33.2, C34.2, C35.2, C36.2, C37.2, C38.2, C39.2, C40.2, C41.2, C42.2, C43.2, C44.2, C45.2, C46.2, C47.2, C48.2, D3.1 (K), D4.1 (K), J1.7, J1.8, J3.1, J4.7, J4.8, J4.9, Q1.3 (S), Q2.3 (S), Q3.3 (S), Q4.3 (S), Q5.3 (S), Q6.3 (S), Q7.3 (S), Q8.3 (S), U1.4 (GND), U2.1 (GND), U3.4 (GND), U4.1 (GND), U5.1 (GND), U6.4 (GND), U7.1 (GND), U8.4 (GND), U9.1 (GND), U10.4 (GND), U11.1 (GND), U12.1 (GND), U13.1 (GND), U14.1 (GND), U15.1 (GND), U16.13 (GND), U17.13 (GND), U18.1 (GND), U19.1 (GND), U20.2 (GND), U21.2 (GND), U22.1 (GND), U23.1 (GND), U24.2 (GND), U25.2 (GND), U26.1 (GND), U27.1 (GND), U28.1 (GND), U29.1 (GND)
IR_sig1: C41.1, R35.2, U16.1 (A0_D0)
IR_sig2: C42.1, R36.2, U16.2 (A1_D1)
IR_sig3: C47.1, R45.2, U16.3 (A2_D2)
IR_sig4: C48.1, R46.2, U16.4 (A3_D3)
unnamed: D1.2 (A), R5.2
unnamed: D1.1 (K), Q1.1 (D)
unnamed: D2.2 (A), R6.2
unnamed: D2.1 (K), Q2.1 (D)
unnamed: D3.2 (A), R15.2
unnamed: D4.2 (A), R16.2
unnamed: D5.2 (A), R17.2
unnamed: D5.1 (K), Q3.1 (D)
unnamed: D6.2 (A), R18.2
unnamed: D6.1 (K), Q4.1 (D)
unnamed: D7.2 (A), R27.2
unnamed: D7.1 (K), Q5.1 (D)
unnamed: D8.2 (A), R28.2
unnamed: D8.1 (K), Q6.1 (D)
unnamed: D9.2 (A), R39.2
unnamed: D9.1 (K), Q7.1 (D)
unnamed: D10.2 (A), R40.2
unnamed: D10.1 (K), Q8.1 (D)
unnamed: Q1.2 (G), R7.2, R9.2
unnamed: Q2.2 (G), R8.2, R10.2
unnamed: Q3.2 (G), R19.2, R21.2
unnamed: Q4.2 (G), R20.2, R22.2
unnamed: Q5.2 (G), R29.2, R31.2
unnamed: Q6.2 (G), R30.2, R32.2
unnamed: Q7.2 (G), R41.2, R43.2
unnamed: Q8.2 (G), R42.2, R44.2
unnamed: C2.1, U4.5 (CONT)
unnamed: R1.2, R3.1, U4.7 (DISCH)
unnamed: R7.1, U4.3 (OUT)
unnamed: C4.1, R1.1, U4.2 (TRIG), U4.6 (THRES)
unnamed: C3.1, U5.5 (CONT)
unnamed: R2.2, R4.1, U5.7 (DISCH)
unnamed: R8.1, U5.3 (OUT)
unnamed: C5.1, R2.1, U5.2 (TRIG), U5.6 (THRES)
unnamed: C14.1, U12.5 (CONT)
unnamed: R11.2, R13.1, U12.7 (DISCH)
unnamed: R19.1, U12.3 (OUT)
unnamed: C17.1, R11.1, U12.2 (TRIG), U12.6 (THRES)
unnamed: C15.1, U13.5 (CONT)
unnamed: R12.2, R14.1, U13.7 (DISCH)
unnamed: R20.1, U13.3 (OUT)
unnamed: C18.1, R12.1, U13.2 (TRIG), U13.6 (THRES)
unnamed: C27.1, U18.5 (CONT)
unnamed: R23.2, R25.1, U18.7 (DISCH)
unnamed: R29.1, U18.3 (OUT)
unnamed: C29.1, R23.1, U18.2 (TRIG), U18.6 (THRES)
unnamed: C28.1, U19.5 (CONT)
unnamed: R24.2, R26.1, U19.7 (DISCH)
unnamed: R30.1, U19.3 (OUT)
unnamed: C30.1, R24.1, U19.2 (TRIG), U19.6 (THRES)
unnamed: R35.1, U20.1 (OUT)
unnamed: R36.1, U21.1 (OUT)
unnamed: C37.1, U22.5 (CONT)
unnamed: R33.2, R37.1, U22.7 (DISCH)
unnamed: R41.1, U22.3 (OUT)
unnamed: C39.1, R33.1, U22.2 (TRIG), U22.6 (THRES)
unnamed: C38.1, U23.5 (CONT)
unnamed: R34.2, R38.1, U23.7 (DISCH)
unnamed: R42.1, U23.3 (OUT)
unnamed: C40.1, R34.1, U23.2 (TRIG), U23.6 (THRES)
unnamed: R45.1, U24.1 (OUT)
unnamed: R46.1, U25.1 (OUT)
RX_{teensy}-TX_{ESP32C301}: J4.6, U16.7 (TX_D6)
RX_{teensy}-TX_{ESP32C302}: J4.14, U17.7 (TX_D6)
RX_{teensy}-TX_{unitV1}: J4.15, U1.1 (TX/G34)
RX_{teensy}-TX_{unitV2}: J4.17, U3.1 (TX/G34)
RX_{teensy}-TX_{unitV3}: J4.4, U6.1 (TX/G34)
RX_{teensy}-TX_{unitV4}: J4.1, U8.1 (TX/G34)
RX_{teensy}-TX_{unitV5}: J4.10, U10.1 (TX/G34)
SCL: J1.5, U16.6 (SCL_D5)
SDA: J1.6, U16.5 (SDA_D4)
SIG_{NeoPixel}: J1.1, U17.11 (MOSI_D10)
SW_{START}: J1.2, J4.11
SW_{TCT1}: J1.4, U16.9 (SCK_D8)
SW_{TCT2}: J1.3, U16.11 (MOSI_D10)
SW_{TGL1}: J2.1, R47.2, U17.6 (SCL_D5)
SW_{TGL2}: J2.2, R48.2, U17.9 (SCK_D8)
TX_{teensy}-RX_{ESP32C301}: J4.5, U16.8 (RX_D7)
TX_{teensy}-RX_{ESP32C302}: J4.13, U17.8 (RX_D7)
TX_{teensy}-RX_{unitV1}: J4.16, U1.2 (RX/G35)
TX_{teensy}-RX_{unitV2}: J4.18, U3.2 (RX/G35)
TX_{teensy}-RX_{unitV3}: J4.3, U6.2 (RX/G35)
TX_{teensy}-RX_{unitV4}: J4.2, U8.2 (RX/G35)
TX_{teensy}-RX_{unitV5}: J4.12, U10.2 (RX/G35)
USS1: U17.1 (A0_D0), U26.2 (Echo)
USS2: U17.2 (A1_D1), U27.2 (Echo)
USS3: U17.3 (A2_D2), U28.2 (Echo)
USS4: U17.4 (A3_D3), U29.2 (Echo)
USS_{EN}: U17.5 (SDA_D4), U26.3 (Trig), U27.3 (Trig), U28.3 (Trig), U29.3 (Trig)

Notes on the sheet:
Camera
SW-SIGNAL_{PULLUP}
3-terminal regulator | 3.3V
3-terminal regulator | 3.3V | UnitV
LED
IR-LED
Connector_{Main}
USS
・D6は起動時にHIGH/LOWしてしまい、 通信していない待機時は常にHIGH ・D8はプログラムの書き込みモードにした際に HIGHになっている必要がある。 書き込みモードへの移行（Bootボタンを押しながらリセットする）を 行う場合は、プルアップ抵抗をつけておくのがベター（らしい） （GPIO8 = 0 & GPIO9 = 0 になると予期せぬ動きをする模様） ・D9はGPIO9とプルアップ抵抗、BOOTボタンに繋がっており、 BOOTボタンを押すとD9がGNDに接続してしまうため、用途は限定的 スイッチ入力に使うのがよさそう
Connector_{Power}
Connector_{NeoPixel}
IR-Receiver

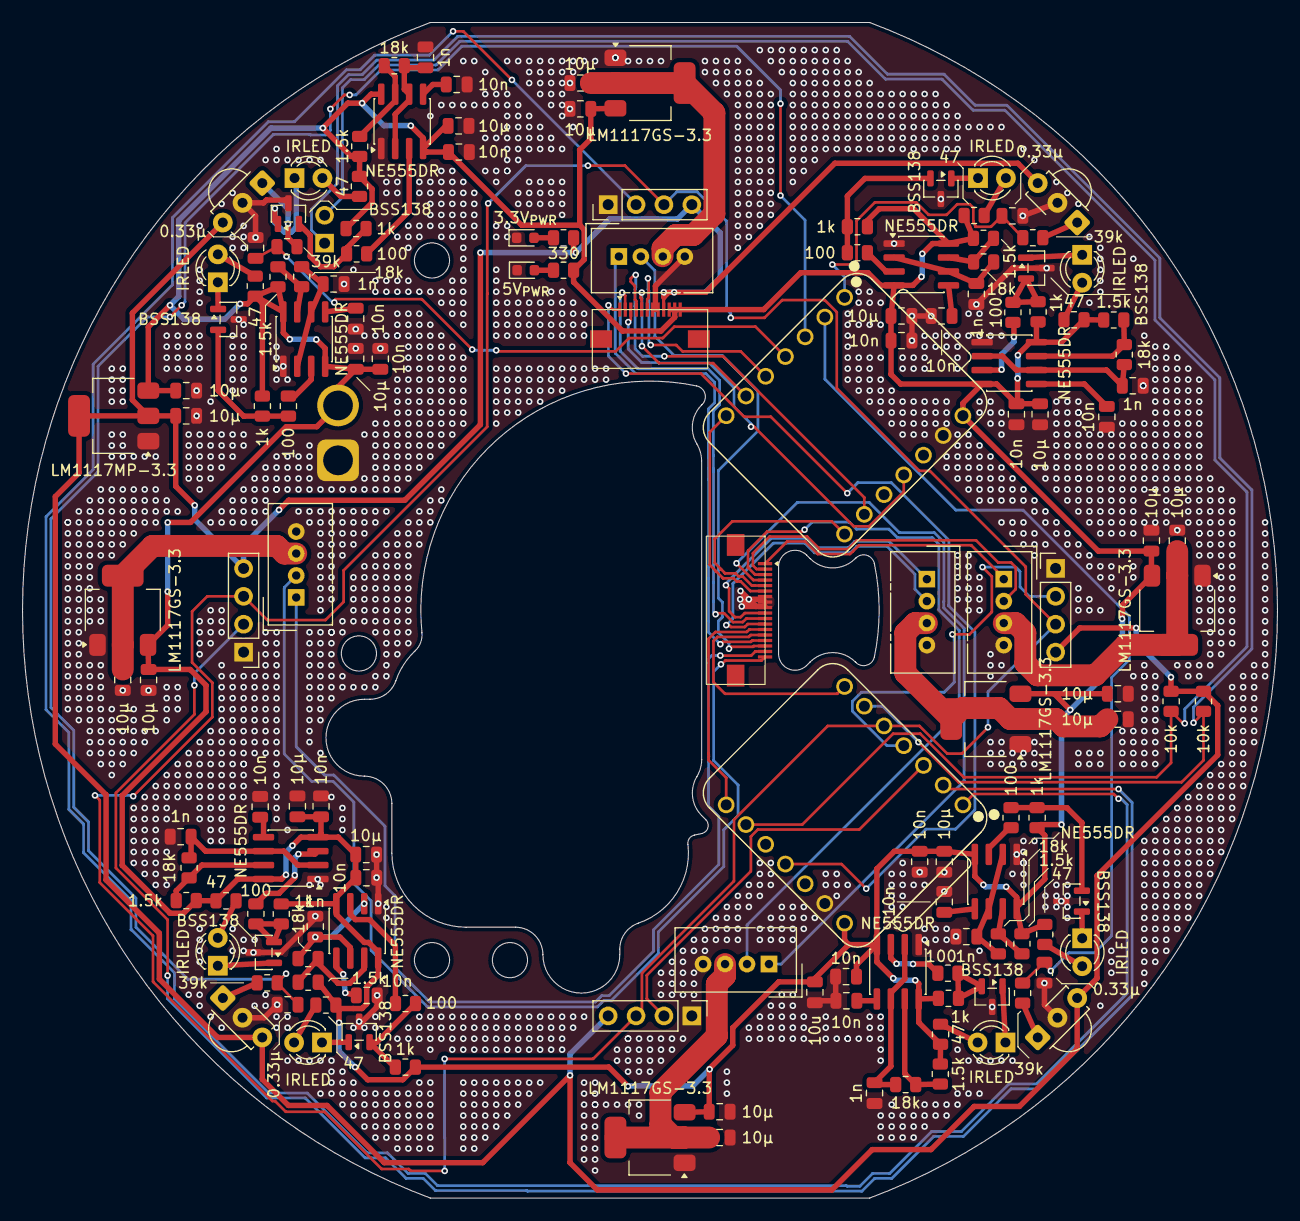
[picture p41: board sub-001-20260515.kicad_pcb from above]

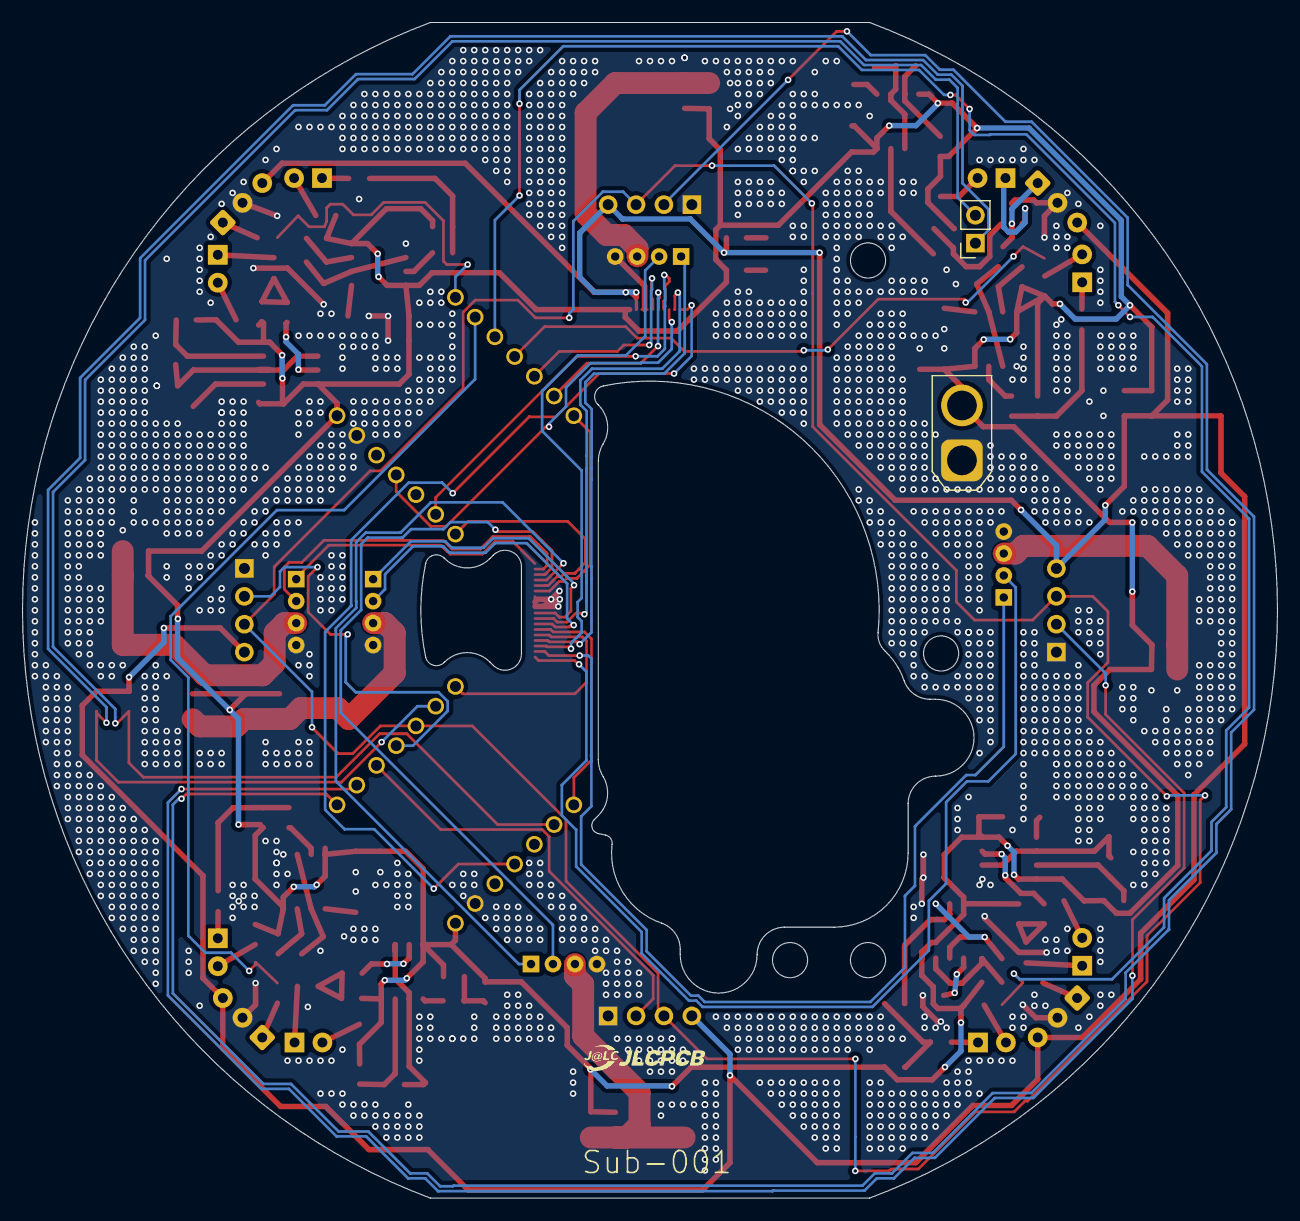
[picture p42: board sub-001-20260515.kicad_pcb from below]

Board: 2 copper layers, 114.3 x 107.0 mm, 147 parts (2 on the bottom side), 101 nets.

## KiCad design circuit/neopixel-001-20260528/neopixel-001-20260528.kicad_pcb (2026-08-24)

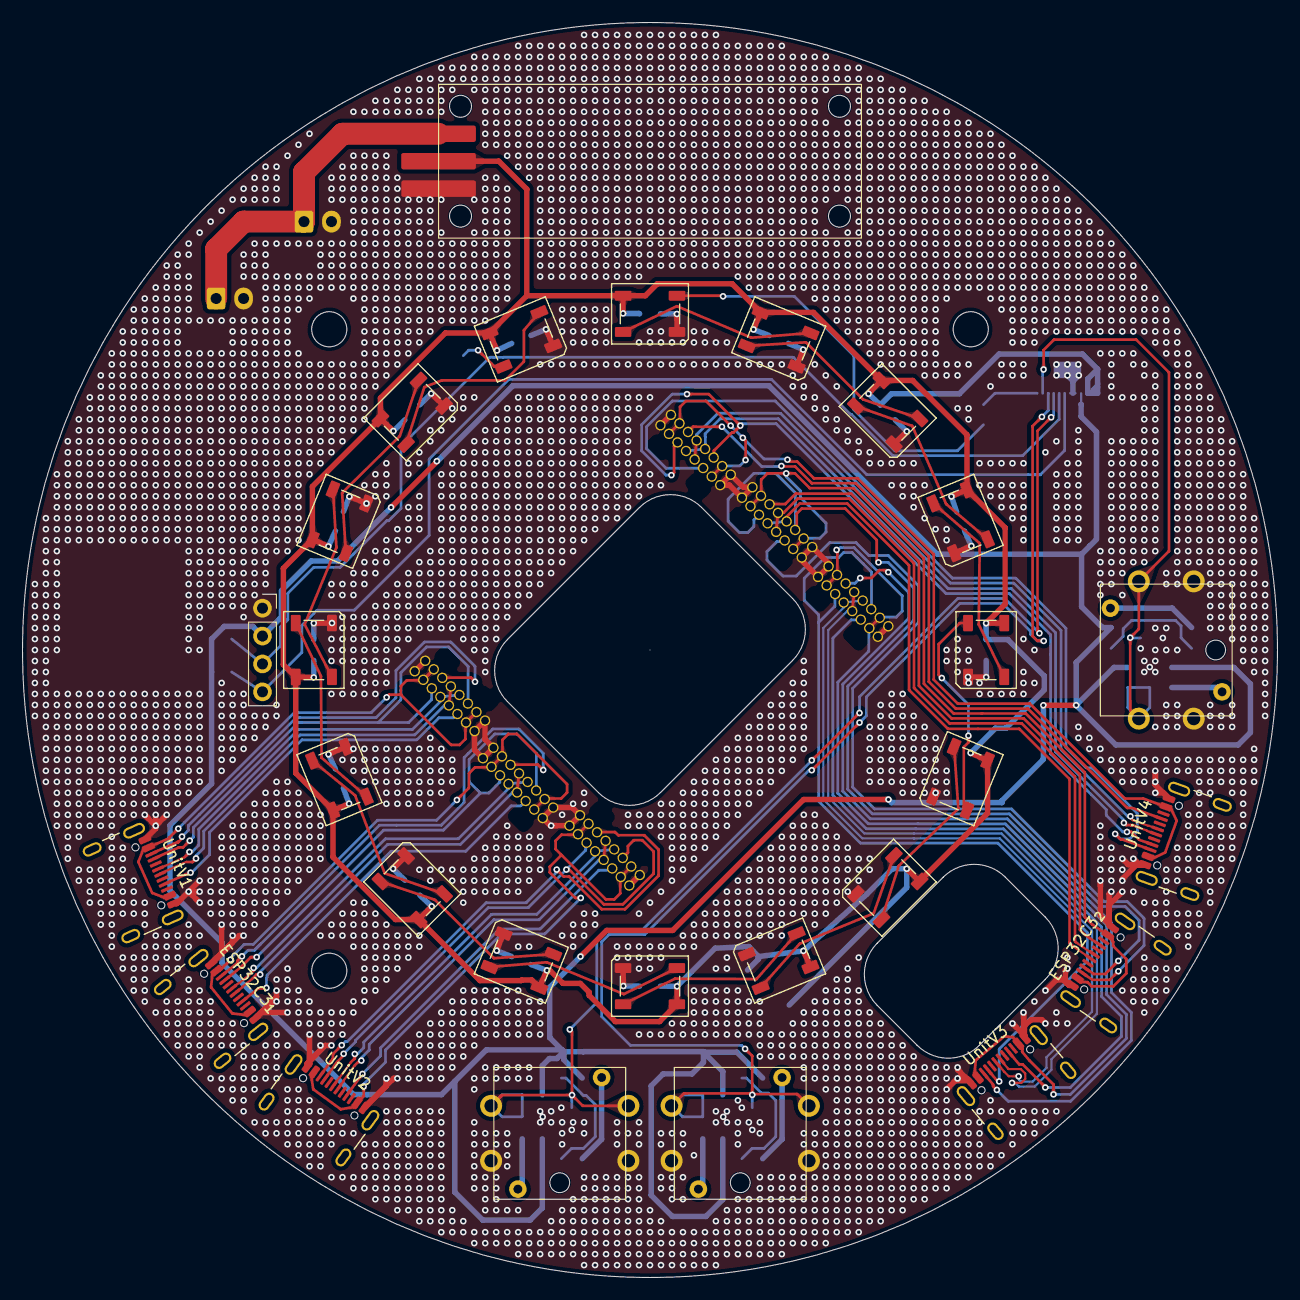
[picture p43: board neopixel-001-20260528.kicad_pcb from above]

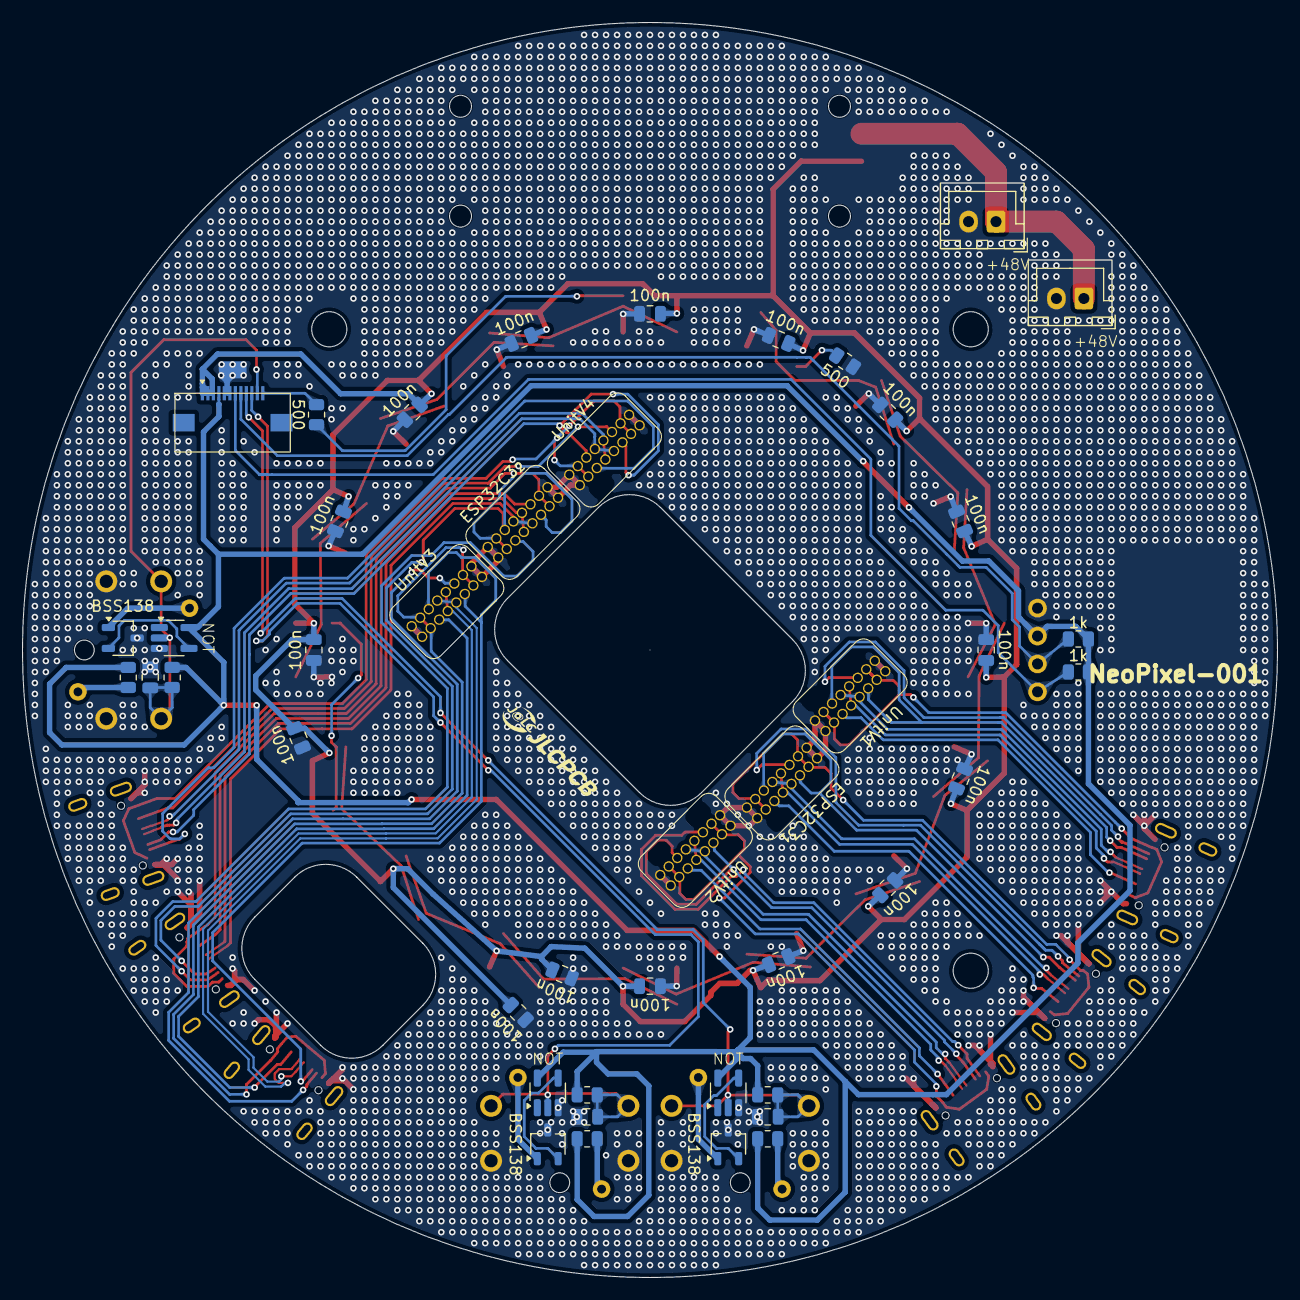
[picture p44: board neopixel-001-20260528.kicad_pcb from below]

Board: 2 copper layers, 114.3 x 114.3 mm, 71 parts (44 on the bottom side), 72 nets.

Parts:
C1, C2, C3, C4, C5, C6, C7, C8, C9, C10, C11, C12, C13, C14, C15, C16, C17, C18, C19: 100n; C_0805_2012Metric
D1, D2, D3, D4, D5, D6, D7, D8, D9, D10, D11, D12, D13, D14, D15, D16: WS2812B; LED_WS2812B_PLCC4_5.0x5.0mm_P3.2mm
J1: Conn_Sub; AFC01-S12FCA-00
J2, J3: Conn_01x02_Pin; JST_XH_B2B-XH-A_1x02_P2.50mm_Vertical
P1: ESP32C3_{1}; USB_C_Receptacle_GCT_USB4105-xx-A_16P_TopMnt_Horizontal
P2: ESP32C3_{1}; USB_Type-C_Vertical_ C6332304
P3: ESP32C3_{2}; USB_C_Receptacle_GCT_USB4105-xx-A_16P_TopMnt_Horizontal
P4: ESP32C3_{2}; USB_Type-C_Vertical_ C6332304
P5: UnitV1; USB_C_Receptacle_GCT_USB4105-xx-A_16P_TopMnt_Horizontal
P6: UnitV1; USB_Type-C_Vertical_ C6332304
P7: UnitV2; USB_C_Receptacle_GCT_USB4105-xx-A_16P_TopMnt_Horizontal
P8: UnitV2; USB_Type-C_Vertical_ C6332304
P9: UnitV3; USB_C_Receptacle_GCT_USB4105-xx-A_16P_TopMnt_Horizontal
P10: UnitV3; USB_Type-C_Vertical_ C6332304
P11: UnitV4; USB_C_Receptacle_GCT_USB4105-xx-A_16P_TopMnt_Horizontal
P12: UnitV4; USB_Type-C_Vertical_ C6332304
Q1, Q2, Q3: BSS138; TSOT-23
R1, R2: 1k; R_0805_2012Metric
R3, R5, R7: 10k; R_0805_2012Metric
R4, R6, R8: 330; R_0805_2012Metric
R9, R10: 500; R_0805_2012Metric
SW1, SW2, SW4: SW_SPST_LED; ST-12-401FC-G
U1: SSD1306; SSD1306_display_module
U2: Aexit_0-50_Voltmeter
U3, U4, U5: 74AHC1G04; SOT-23-5_HandSoldering

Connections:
+3.3V: J1.4, R1.2, R2.2, R3.2, R4.2, R5.2, R6.2, R7.2, R8.2, U1.2 (VCC), U3.5 (VCC), U4.5 (VCC), U5.5 (VCC)
+5V: C1.1, C2.1, C3.1, C4.1, C5.1, C6.1, C7.1, C8.1, C9.1, C10.1, C11.1, C12.1, C13.1, C14.1, C15.1, C16.1, D1.1 (VDD), D2.1 (VDD), D3.1 (VDD), D4.1 (VDD), D5.1 (VDD), D6.1 (VDD), D7.1 (VDD), D8.1 (VDD), D9.1 (VDD), D10.1 (VDD), D11.1 (VDD), D12.1 (VDD), D13.1 (VDD), D14.1 (VDD), D15.1 (VDD), D16.1 (VDD), J1.1, J1.2, J1.3, U2.2 (V_{logic})
+48V: J2.1, J3.1, U2.1 (V_{Power})
GND: C1.2, C2.2, C3.2, C4.2, C5.2, C6.2, C7.2, C8.2, C9.2, C10.2, C11.2, C12.2, C13.2, C14.2, C15.2, C16.2, C17.1, C18.1, C19.1, D1.3 (VSS), D2.3 (VSS), D3.3 (VSS), D4.3 (VSS), D5.3 (VSS), D6.3 (VSS), D7.3 (VSS), D8.3 (VSS), D9.3 (VSS), D10.3 (VSS), D11.3 (VSS), D12.3 (VSS), D13.3 (VSS), D14.3 (VSS), D15.3 (VSS), D16.3 (VSS), J1.5, J1.6, J2.2, J3.2, P1.A1 (GND), P1.A12 (GND), P1.B1 (GND), P1.B12 (GND), P2.A1 (GND), P3.A1 (GND), P3.A12 (GND), P3.B1 (GND), P3.B12 (GND), P4.A1 (GND), P5.A1 (GND), P5.A12 (GND), P5.B1 (GND), P5.B12 (GND), P6.A1 (GND), P7.A1 (GND), P7.A12 (GND), P7.B1 (GND), P7.B12 (GND), P8.A1 (GND), P9.A1 (GND), P9.A12 (GND), P9.B1 (GND), P9.B12 (GND), P10.A1 (GND), P11.A1 (GND), P11.A12 (GND), P11.B1 (GND), P11.B12 (GND), P12.A1 (GND), Q1.3 (S), Q2.3 (S), Q3.3 (S), R10.2, SW1.1, SW2.1, SW4.1, U1.1 (GND), U2.3 (GND), U3.3 (GND), U4.3 (GND), U5.3 (GND)
unnamed: D1.4 (DIN), R9.2
unnamed: D1.2 (DOUT), D2.4 (DIN)
unnamed: D2.2 (DOUT), D3.4 (DIN)
unnamed: D3.2 (DOUT), D4.4 (DIN)
unnamed: D4.2 (DOUT), D5.4 (DIN)
unnamed: D5.2 (DOUT), D6.4 (DIN)
unnamed: D6.2 (DOUT), D7.4 (DIN)
unnamed: D7.2 (DOUT), D8.4 (DIN)
unnamed: D8.2 (DOUT), D9.4 (DIN)
unnamed: D9.2 (DOUT), D10.4 (DIN)
unnamed: D10.2 (DOUT), D11.4 (DIN)
unnamed: D11.2 (DOUT), D12.4 (DIN)
unnamed: D12.2 (DOUT), D13.4 (DIN)
unnamed: D13.2 (DOUT), D14.4 (DIN)
unnamed: D14.2 (DOUT), D15.4 (DIN)
unnamed: D15.2 (DOUT), D16.4 (DIN)
unnamed: D16.2 (DOUT), R10.1
unnamed: Q1.1 (D), SW1.3 (K)
unnamed: Q1.2 (G), U3.4
unnamed: Q2.1 (D), SW2.3 (K)
unnamed: Q2.2 (G), U4.4
unnamed: Q3.1 (D), SW4.3 (K)
unnamed: Q3.2 (G), U5.4
unnamed: R4.1, SW1.4 (A)
unnamed: R6.1, SW2.4 (A)
unnamed: R8.1, SW4.4 (A)
P1_CC: P1.A5 (CC), P2.A5 (CC)
P1_D+: P1.A7 (D-), P2.A7 (D-)
P1_D-: P1.A6 (D+), P2.A6 (D+)
P1_SBU1: P1.A8 (SBU1), P2.A8 (SBU1)
P1_SBU2: P1.B8 (SBU2), P2.B8 (SBU2)
P1_VBUS: P1.A4 (VBUS), P1.A9 (VBUS), P1.B4 (VBUS), P1.B9 (VBUS), P2.A4 (VBUS)
P2_CC: P3.A5 (CC), P4.A5 (CC)
P2_D+: P3.A7 (D-), P4.A7 (D-)
P2_D-: P3.A6 (D+), P4.A6 (D+)
P2_SBU1: P3.A8 (SBU1), P4.A8 (SBU1)
P2_SBU2: P3.B8 (SBU2), P4.B8 (SBU2)
P2_VBUS: P3.A4 (VBUS), P3.A9 (VBUS), P3.B4 (VBUS), P3.B9 (VBUS), P4.A4 (VBUS)
P3_CC: P5.A5 (CC), P6.A5 (CC)
P3_D+: P5.A7 (D-), P6.A7 (D-)
P3_D-: P5.A6 (D+), P6.A6 (D+)
P3_SBU1: P5.A8 (SBU1), P6.A8 (SBU1)
P3_SBU2: P5.B8 (SBU2), P6.B8 (SBU2)
P3_VBUS: P5.A4 (VBUS), P5.A9 (VBUS), P5.B4 (VBUS), P5.B9 (VBUS), P6.A4 (VBUS)
P4_CC: P7.A5 (CC), P8.A5 (CC)
P4_D+: P7.A7 (D-), P8.A7 (D-)
P4_D-: P7.A6 (D+), P8.A6 (D+)
P4_SBU1: P7.A8 (SBU1), P8.A8 (SBU1)
P4_SBU2: P7.B8 (SBU2), P8.B8 (SBU2)
P4_VBUS: P7.A4 (VBUS), P7.A9 (VBUS), P7.B4 (VBUS), P7.B9 (VBUS), P8.A4 (VBUS)
P5_CC: P9.A5 (CC), P10.A5 (CC)
P5_D+: P9.A7 (D-), P10.A7 (D-)
P5_D-: P9.A6 (D+), P10.A6 (D+)
P5_SBU1: P9.A8 (SBU1), P10.A8 (SBU1)
P5_SBU2: P9.B8 (SBU2), P10.B8 (SBU2)
P5_VBUS: P9.A4 (VBUS), P9.A9 (VBUS), P9.B4 (VBUS), P9.B9 (VBUS), P10.A4 (VBUS)
P6_CC: P11.A5 (CC), P12.A5 (CC)
P6_D+: P11.A7 (D-), P12.A7 (D-)
P6_D-: P11.A6 (D+), P12.A6 (D+)
P6_SBU1: P11.A8 (SBU1), P12.A8 (SBU1)
P6_SBU2: P11.B8 (SBU2), P12.B8 (SBU2)
P6_VBUS: P11.A4 (VBUS), P11.A9 (VBUS), P11.B4 (VBUS), P11.B9 (VBUS), P12.A4 (VBUS)
SCL: J1.8, R2.1, U1.3 (SCL)
SDA: J1.7, R1.1, U1.4 (SDA)
SIG_{NeoPixel}: J1.12, R9.1
SW_{START}: C19.2, J1.11, R7.1, SW4.2, U5.2
SW_{TCT1}: C17.2, J1.9, R3.1, SW1.2, U3.2
SW_{TCT2}: C18.2, J1.10, R5.1, SW2.2, U4.2

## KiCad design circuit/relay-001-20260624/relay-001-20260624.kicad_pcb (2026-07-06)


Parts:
J1: Dribbler_{Back}; PinHeader_1x03_P2.54mm_Vertical
J2: Kicker-Board; PinSocket_2x05_P2.54mm_Vertical
J3: MD_{Signal}; PinSocket_2x08_P2.54mm_Horizontal
J4: Main-Board; PinSocket_2x09_P2.54mm_Vertical
J5: Power_{5V}; AMASS_XT30U-M_1x02_P5.0mm_Vertical
J6: Power_{VCC}; AMASS_XT30U-M_1x02_P5.0mm_Vertical
J7: Power_{Logic}; AMASS_XT30U-M_1x02_P5.0mm_Vertical
J8: Line_{Power}; AMASS_XT30U-M_1x02_P5.0mm_Vertical
J9: Line_{UART}; JST_XH_B2B-XH-A_1x02_P2.50mm_Vertical
J10: MD_{Power}; AMASS_XT30PW-M_1x02_P2.50mm_Horizontal
J11: Motor1; JST_XH_B2B-XH-A_1x02_P2.50mm_Vertical
J12: Motor2; JST_XH_B2B-XH-A_1x02_P2.50mm_Vertical
J13: Motor3; JST_XH_B2B-XH-A_1x02_P2.50mm_Vertical
J14: Motor4; JST_XH_B2B-XH-A_1x02_P2.50mm_Vertical
J15: Voltmeter; JST_XH_B2B-XH-A_1x02_P2.50mm_Vertical

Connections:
+3.3V: J1.2, J2.9, J3.16, J4.9, J7.1
+5V: J4.12, J7.2
+5V_{Line}: J5.2, J8.2
BallCatch_{Back}: J3.2, J4.14
BallCatch_{Front}: J2.8, J4.11
Dribbler_{Back}: J1.1, J4.15
EN_{Boost}: J2.1, J4.18
EN_{Dribbler-Front}: J2.4, J4.8
GND: J1.3, J2.2, J2.10, J3.14, J4.13, J5.1, J6.1, J8.1, J10.1, J15.2
Kick_{Chip}: J2.3, J4.16
Kick_{Stroke}: J2.7, J4.17
Motor1_{PWM}: J3.10, J4.3
Motor2_{PWM}: J3.8, J4.5
Motor3_{PWM}: J3.6, J4.7
Motor4_{PWM}: J3.4, J4.10
Motor_{EN}: J3.12, J4.1
Motor_{OUT1-1}: J3.15, J11.1
Motor_{OUT1-2}: J3.13, J11.2
Motor_{OUT2-1}: J3.11, J12.1
Motor_{OUT2-2}: J3.9, J12.2
Motor_{OUT3-1}: J3.7, J13.1
Motor_{OUT3-2}: J3.5, J13.2
Motor_{OUT4-1}: J3.3, J14.1
Motor_{OUT4-2}: J3.1, J14.2
PH_{Dribbler-Front}: J2.6, J4.6
RX_{teensy}-TX_{Arduino}-5V: J4.4, J9.2
TX_{teensy}-RX_{Arduino}-5V: J4.2, J9.1
VCC: J2.5, J6.2, J10.2, J15.1


Board: 2 copper layers, 169.0 x 126.3 mm, 15 parts (0 on the bottom side), 28 nets.

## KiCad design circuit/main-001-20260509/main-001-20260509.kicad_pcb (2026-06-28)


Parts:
BZ1: Buzzer; PKM13EPYH4000-A0
C1, C2: 100n; C_0805_2012Metric
D1: D13; LED_0603_1608Metric
J1: Conn_Relay; PinHeader_2x09_P2.54mm_Vertical
J2: Conn_Sub; AFC01-S18FCA-00
Q1, Q2: BSS138; SOT-23
R1, R2, R3, R4, R8: 10k; R_0805_2012Metric
R5, R6, R7: 1k; R_0805_2012Metric
R9: 330; R_0805_2012Metric
SW1: RESET; TVBP06-B043C
U1: DEV-16771
U2: BNO055

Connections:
+3.3V: C1.1, J1.9, Q1.1 (G), Q2.1 (G), R1.1, R2.1, R5.1, R7.1, R8.1, U2.1 (VIN)
+5V: J1.12, R3.1, R4.1, U1.VIN
BallCatch_{Back}: J1.14, U1.27 (A13)
BallCatch_{Front}: J1.11, U1.26 (A12)
Buzzer: R6.2, U1.2 (OUT2)
Dribbler_{Back}: J1.15, U1.36 (CS2)
EN_{Boost}: J1.18, U1.32 (OUT1B)
EN_{Dribbler-Front}: J1.8, U1.22 (A8)
GND: BZ1.2 (-), C1.2, C2.2, D1.1 (K), J1.13, J2.10, J2.11, J2.12, SW1.2 (B), U1.GND, U2.2 (GND), U2.7 (GND)
Kick_{Chip}: J1.16, U1.31 (CTX3)
Kick_{Stroke}: J1.17, U1.30 (CRX3)
LED: R9.1, U1.33 (MCLK2)
Main_RST: C2.1, R8.2, SW1.1 (A), U1.PROGRAM
Motor1_{PWM}: J1.3, U1.9 (OUT1C)
Motor2_{PWM}: J1.5, U1.10 (CS1)
Motor3_{PWM}: J1.7, U1.11 (MOSI)
Motor4_{PWM}: J1.10, U1.12 (MISO)
Motor_{EN}: J1.1, U1.6 (OUT1D)
unnamed: BZ1.1 (+), R6.1
unnamed: D1.2 (A), R9.2
PH_{Dribbler-Front}: J1.6, U1.23 (A9)
RX_{teensy}-TX_{Arduino}-3V3: Q1.2 (S), R1.2, U1.0 (RX1)
RX_{teensy}-TX_{Arduino}-5V: J1.4, Q1.3 (D), R3.2
RX_{teensy}-TX_{ESP32C301}: J2.13, U1.7 (RX2)
RX_{teensy}-TX_{ESP32C302}: J2.5, U1.15 (A1)
RX_{teensy}-TX_{unitV1}: J2.4, U1.16 (A2)
RX_{teensy}-TX_{unitV2}: J2.2, U1.21 (A7)
RX_{teensy}-TX_{unitV3}: J2.15, U1.25 (A11)
RX_{teensy}-TX_{unitV4}: J2.18, U1.28 (RX7)
RX_{teensy}-TX_{unitV5}: J2.9, U1.34 (RX8)
SCL: R7.2, U1.19 (A5), U2.4 (SCL/R)
SDA: R5.2, U1.18 (A4), U2.3 (SDA/T)
SW_{START}: J2.8, U1.5 (IN2)
TX_{teensy}-RX_{Arduino}-3V3: Q2.2 (S), R2.2, U1.1 (TX1)
TX_{teensy}-RX_{Arduino}-5V: J1.2, Q2.3 (D), R4.2
TX_{teensy}-RX_{ESP32C301}: J2.14, U1.8 (TX2)
TX_{teensy}-RX_{ESP32C302}: J2.6, U1.14 (A0)
TX_{teensy}-RX_{unitV1}: J2.3, U1.17 (A3)
TX_{teensy}-RX_{unitV2}: J2.1, U1.20 (A6)
TX_{teensy}-RX_{unitV3}: J2.16, U1.24 (A10)
TX_{teensy}-RX_{unitV4}: J2.17, U1.29 (TX7)
TX_{teensy}-RX_{unitV5}: J2.7, U1.35 (TX8)

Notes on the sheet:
Connector_Sub
BNO055
LED
Teensy4.1
Connector_Relay
RESET_BTN
Buzzer
Level-Conversion



Board: 2 copper layers, 43.3 x 63.0 mm, 20 parts (3 on the bottom side), 42 nets.

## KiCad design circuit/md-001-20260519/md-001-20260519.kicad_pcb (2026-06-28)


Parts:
C1, C2, C5, C6: 22n; R_0805_2012Metric
C3, C4, C7, C8: 220n; R_0805_2012Metric
C9, C10, C11, C12, C13: 100n; R_0805_2012Metric
C14: 100μ; R_1206_3216Metric
D1: MTR_PWR; LED_0603_1608Metric
D2: LGC_PWR; LED_0603_1608Metric
J1: VIN-motor; AMASS_XT30PW-F_1x02_P2.50mm_Horizontal
J2: Conn_Ball_Catch; PinSocket_1x03_P2.54mm_Vertical
J3: Conn_relay; PinHeader_2x08_P2.54mm_Horizontal
R1, R2, R9, R10: 10k; R_0805_2012Metric
R3, R5, R11, R13: NP; R_0805_2012Metric; not fitted
R4, R6, R12, R14: 20k; R_0805_2012Metric
R7, R8, R15, R16, R17: 2.49k; R_0805_2012Metric
R18: 330; R_0805_2012Metric
U1, U2, U3, U4: HTSSOP-16-1EP_4.4x5mm_P0.65mm_EP3.4x5mm_Mask2.66x2.46mm

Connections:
+3.3V: C9.1, C10.1, C11.1, C12.1, J2.2, J3.16, R1.1, R2.1, R9.1, R10.1, R18.1, U1.3 (SLEEP), U2.3 (SLEEP), U3.3 (SLEEP), U4.3 (SLEEP)
BallCatch_{Back}: J2.1, J3.2
GND: C9.2, C10.2, C11.2, C12.2, C13.2, C14.2, D1.1 (K), D2.1 (K), J1.1, J2.3, J3.14, R3.2, R4.2, R5.2, R6.2, R7.2, R8.2, R11.2, R12.2, R13.2, R14.2, R15.2, R16.2, U1.9 (PGND), U1.15 (GND), U1.16 (PMODE), U1.17 (GND), U2.9 (PGND), U2.15 (GND), U2.16 (PMODE), U2.17 (GND), U3.9 (PGND), U3.15 (GND), U3.16 (PMODE), U3.17 (GND), U4.9 (PGND), U4.15 (GND), U4.16 (PMODE), U4.17 (GND)
IMODE-1: R4.1, U1.7 (IMODE)
IMODE-2: R6.1, U2.7 (IMODE)
IMODE-3: R12.1, U3.7 (IMODE)
IMODE-4: R14.1, U4.7 (IMODE)
Motor1_{PWM}: J3.10, U1.2 (PH)
Motor2_{PWM}: J3.8, U2.2 (PH)
Motor3_{PWM}: J3.6, U3.2 (PH)
Motor4_{PWM}: J3.4, U4.2 (PH)
Motor_{EN}: J3.12, U1.1 (EN), U2.1 (EN), U3.1 (EN), U4.1 (EN)
Motor_{OUT1-1}: J3.15, U1.8 (OUT1)
Motor_{OUT1-2}: J3.13, U1.10 (OUT2)
Motor_{OUT2-1}: J3.11, U2.8 (OUT1)
Motor_{OUT2-2}: J3.9, U2.10 (OUT2)
Motor_{OUT3-1}: J3.7, U3.8 (OUT1)
Motor_{OUT3-2}: J3.5, U3.10 (OUT2)
Motor_{OUT4-1}: J3.3, U4.8 (OUT1)
Motor_{OUT4-2}: J3.1, U4.10 (OUT2)
unnamed: D1.2 (A), R17.2
unnamed: D2.2 (A), R18.2
unnamed: C1.2, U1.13 (CPH)
unnamed: C1.1, U1.14 (CPL)
unnamed: R7.1, U1.6 (IPROPI)
unnamed: C3.1, U1.12 (VCP)
unnamed: C2.2, U2.13 (CPH)
unnamed: C2.1, U2.14 (CPL)
unnamed: R8.1, U2.6 (IPROPI)
unnamed: C4.1, U2.12 (VCP)
unnamed: C5.2, U3.13 (CPH)
unnamed: C5.1, U3.14 (CPL)
unnamed: R15.1, U3.6 (IPROPI)
unnamed: C7.1, U3.12 (VCP)
unnamed: C6.2, U4.13 (CPH)
unnamed: C6.1, U4.14 (CPL)
unnamed: R16.1, U4.6 (IPROPI)
unnamed: C8.1, U4.12 (VCP)
VCC: C3.2, C4.2, C7.2, C8.2, C13.1, C14.1, J1.2, R17.1, U1.11 (VM), U2.11 (VM), U3.11 (VM), U4.11 (VM)
VREF-1: R1.2, R3.1, U1.5 (VREF)
VREF-2: R2.2, R5.1, U2.5 (VREF)
VREF-3: R9.2, R11.1, U3.5 (VREF)
VREF-4: R10.2, R13.1, U4.5 (VREF)

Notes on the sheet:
MD1
Connector | BallCatch
MD4
POWER INPUT
Connector | Relay
MD3
【確認事項】 ・モーター出力ピンにノイズ除去用の コンデンサ（10nF-100nF）をかませるか ・2.54mmピッチのピンソケット/ヘッダの定格電流 ＝3.0A
LED
MD2



Board: 4 copper layers, 71.4 x 21.3 mm, 41 parts (32 on the bottom side), 43 nets.

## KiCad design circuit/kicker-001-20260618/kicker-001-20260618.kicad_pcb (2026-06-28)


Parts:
C1: 47μ; C_0805_2012Metric
C2, C6: 1μ; C_0805_2012Metric
C3, C4, C5, C11, C12: 100n; C_0805_2012Metric
C7, C8: 10μ; C_0805_2012Metric
C9: 22n; C_0805_2012Metric
C10: 220n; C_0805_2012Metric
D1: LED; LED_D3.0mm
D2: CUHS20F60
D3: PWR; LED_0603_1608Metric
D4: LGC; LED_0603_1608Metric
J1: Solenoid_{Stroke}; JST_XH_B2B-XH-A_1x02_P2.50mm_Vertical
J2: Solenoid_{Chip}; JST_XH_B2B-XH-A_1x02_P2.50mm_Vertical
J3: Drribler_{Front}; JST_XH_B2B-XH-A_1x02_P2.50mm_Vertical
J4: Conn_Relay; PinHeader_2x05_P2.54mm_Vertical
J6: Voltmeter; JST_XH_B2B-XH-A_1x02_P2.50mm_Vertical
JP1, JP3: _{ON}; SolderJumper-2_P1.3mm_Open_RoundedPad1.0x1.5mm
JP2, JP4: _{OFF}; SolderJumper-2_P1.3mm_Open_RoundedPad1.0x1.5mm
L1: 33μ; SRC1317
Q1: BSS138; TSOT-23
Q2: TJ15S06M3L; TO-252-2
Q3: Q_Photo_CE; NJL7502L
Q4, Q5: MTB010N06RJ3; TO-252-2
R1: 100; R_0805_2012Metric
R2, R3, R4, R5, R6, R13: 10k; R_0805_2012Metric
R7: 1k; R_0805_2012Metric
R8: 75; R_0805_2012Metric
R9: 36k; R_0805_2012Metric
R10, R15: 2.49k; R_0805_2012Metric
R11, R12: 100k; R_0805_2012Metric
R14: NP; R_0805_2012Metric; not fitted
R16: 330; R_0805_2012Metric
R17: 20k; R_0805_2012Metric
U1, U4, U5, U7, U8: NOT; SOT-23-5_HandSoldering
U2, U9, U10: TLP2361; SO-5-6_4.55x3.7mm_P1.27mm
U3: XL6009E1; TO-263-5_TabPin3
U6: DRV8874; HTSSOP-16-1EP_4.4x5mm_P0.65mm_EP3.4x5mm_Mask2.66x2.46mm
U11, U12: AND; SOT-23-5_HandSoldering

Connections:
+3.3V: C5.1, C11.1, C12.1, J4.9, Q3.1 (C), R8.2, R13.1, R16.1, U1.5 (VCC), U2.6 (VCC), U4.5 (VCC), U5.5 (VCC), U6.3 (SLEEP), U7.5 (VCC), U8.5 (VCC), U9.6 (VCC), U10.6 (VCC), U11.5 (VCC), U12.5 (VCC)
+48V: C6.1, D2.1 (K), J1.1, J2.2, J6.1, R9.2
BallCatch_{Front}: J4.8, Q3.2 (E), R4.1
EN_{BOOST}: J4.1, U1.2
EN_{Dribbler-Front}: J4.4, U6.1 (EN)
GND: C1.2, C2.2, C3.2, C4.2, C5.2, C6.2, C7.2, C8.2, C11.2, C12.2, D1.2 (K), D3.1 (K), D4.1 (K), J4.2, J4.10, J6.2, Q1.2 (S), Q4.3 (S), Q5.3 (S), R2.1, R4.2, R5.2, R6.2, R7.2, R10.1, R14.2, R17.2, U1.3 (GND), U2.3 (Cathode), U2.4 (GND), U3.1 (GND), U4.3 (GND), U5.3 (GND), U6.9 (PGND), U6.15 (GND), U6.16 (PMODE), U6.17 (GND), U7.3 (GND), U8.3 (GND), U9.3 (Cathode), U9.4 (GND), U10.3 (Cathode), U10.4 (GND), U11.3 (GND), U12.3 (GND)
IMODE_{Dribbler-Front}: R17.1, U6.7 (IMODE)
Kick_{Chip}: J4.3, JP3.1 (A), JP4.1 (A), U12.1
Kick_{Stroke}: J4.7, JP1.1 (A), JP2.1 (A), U11.1
NMOS^{D}_{BOOST-Chip}: J2.1, Q5.2 (D)
NMOS^{D}_{BOOST-Stroke}: J1.2, Q4.2 (D)
unnamed: C7.1, R11.2, U7.2
unnamed: C8.1, R12.2, U8.2
unnamed: D1.1 (A), R8.1
unnamed: D2.2 (A), L1.2, U3.3 (SW)
unnamed: D3.2 (A), R15.2
unnamed: D4.2 (A), R16.2
unnamed: JP1.2 (B), R11.1
unnamed: JP3.2 (B), R12.1
unnamed: Q1.3 (D), Q2.1 (G), R3.2
unnamed: Q1.1 (G), R1.2, R2.2
unnamed: U1.4, U2.1 (Anode)
unnamed: R7.1, R9.1, U3.5 (FB)
unnamed: C9.2, U6.13 (CPH)
unnamed: C9.1, U6.14 (CPL)
unnamed: R10.2, U6.6 (IPROPI)
unnamed: C10.1, U6.12 (VCP)
unnamed: U4.4, U9.1 (Anode)
unnamed: U5.4, U10.1 (Anode)
unnamed: U7.4, U11.2
unnamed: U8.4, U12.2
OUT1_{Dribbler-Front}: J3.2, U6.8 (OUT1)
OUT2_{Dribbler-Front}: J3.1, U6.10 (OUT2)
PH_{Dribbler-Front}: J4.6, U6.2 (PH)
VCC: C10.2, J4.5, Q2.2 (D), R3.1, R15.1, U6.11 (VM)
VREF_{Dribbler-Front}: R13.2, R14.1, U6.5 (VREF)
^{ONESHOT}Kick_{Chip}: JP4.2 (B), U5.2, U12.4
^{ONESHOT}Kick_{Stroke}: JP2.2 (B), U4.2, U11.4
^{SAFE}EN_{BOOST}: R1.1, U2.5 (Vo)
^{SAFE}Kick_{Chip}: C4.1, Q5.1 (G), R6.1, U10.5 (Vo)
^{SAFE}Kick_{Stroke}: C3.1, Q4.1 (G), R5.1, U9.5 (Vo)
^{SAFE}VCC: C1.1, C2.1, L1.1, Q2.3 (S), U3.2 (EN), U3.4 (VIN)

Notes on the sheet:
BallCatch_{Front}
Connector_{Solenoid}
Connector_{Voltmeter}
t_{s} = -R_{Ω}C_{F}×ln(1-(V_{TH}/V_{H})) t_{s} = -100*10^{3}×10*10^{-6}×ln(1-(2.1/3.3)) ≒ 1.011..._{s}
EN_{BOOST}
NMOS
Protection_{EN_BOOST}
Oneshot Circuit
Protection_{Kick}
MD_{Dribbler-Front}
MOSFETのシンボルとフットプリントの連携をする際 必ずDS上のMechanicalなPinAssignとSymbolのPinAssignが 対応しているかを確認すること、しないと燃える！
LED
BOOST
Connector_{Dribbler-Front}
Connector_{Relay}



Board: 2 copper layers, 71.4 x 59.3 mm, 60 parts (34 on the bottom side), 42 nets.

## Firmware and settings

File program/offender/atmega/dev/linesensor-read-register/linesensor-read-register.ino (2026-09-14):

#include <Arduino.h>
#include <stdint.h>

// ============================================================
// 32個のセンサ入力
//
// bit  0 : PB7
// bit  1 : PB6
// bit  2 : PB5
// bit  3 : PB4
// bit  4 : PB0
// bit  5 : PH6
// bit  6 : PH5
// bit  7 : PH4
// bit  8 : PH3
// bit  9 : PH2
// bit 10 : PF6
// bit 11 : PF7
// bit 12 : PA1
// bit 13 : PA2
// bit 14 : PJ6
// bit 15 : PJ5
// bit 16 : PJ4
// bit 17 : PJ3
// bit 18 : PC5
// bit 19 : PC4
// bit 20 : PC3
// bit 21 : PC2
// bit 22 : PC1
// bit 23 : PC0
// bit 24 : PG1
// bit 25 : PG0
// bit 26 : PL3
// bit 27 : PL2
// bit 28 : PL1
// bit 29 : PL0
// bit 30 : PG3
// bit 31 : PH7
//
// 物理HIGH -> 1
// 物理LOW  -> 0
// ============================================================


// ============================================================
// センサ入力をINPUT_PULLUPに設定
// ============================================================
void initSensors()
{
    // --------------------------------------------------------
    // PORTB
    // PB7, PB6, PB5, PB4, PB0
    // --------------------------------------------------------
    constexpr uint8_t MASK_B =
        (1 << PB7) |
        (1 << PB6) |
        (1 << PB5) |
        (1 << PB4) |
        (1 << PB0);

    DDRB  &= ~MASK_B;   // INPUT
    PORTB |=  MASK_B;   // PULLUP ON


    // --------------------------------------------------------
    // PORTH
    // PH6, PH5, PH4, PH3, PH2, PH7
    // --------------------------------------------------------
    constexpr uint8_t MASK_H =
        (1 << PH6) |
        (1 << PH5) |
        (1 << PH4) |
        (1 << PH3) |
        (1 << PH2) |
        (1 << PH7);

    DDRH  &= ~MASK_H;   // INPUT
    PORTH |=  MASK_H;   // PULLUP ON


    // --------------------------------------------------------
    // PORTF
    // PF6, PF7
    // --------------------------------------------------------
    constexpr uint8_t MASK_F =
        (1 << PF6) |
        (1 << PF7);

    DDRF  &= ~MASK_F;   // INPUT
    PORTF |=  MASK_F;   // PULLUP ON


    // --------------------------------------------------------
    // PORTA
    // PA1, PA2
    // --------------------------------------------------------
    constexpr uint8_t MASK_A =
        (1 << PA1) |
        (1 << PA2);

    DDRA  &= ~MASK_A;   // INPUT
    PORTA |=  MASK_A;   // PULLUP ON


    // --------------------------------------------------------
    // PORTJ
    // PJ6, PJ5, PJ4, PJ3
    // --------------------------------------------------------
    constexpr uint8_t MASK_J =
        (1 << PJ6) |
        (1 << PJ5) |
        (1 << PJ4) |
        (1 << PJ3);

    DDRJ  &= ~MASK_J;   // INPUT
    PORTJ |=  MASK_J;   // PULLUP ON


    // --------------------------------------------------------
    // PORTC
    // PC5, PC4, PC3, PC2, PC1, PC0
    // --------------------------------------------------------
    constexpr uint8_t MASK_C =
        (1 << PC5) |
        (1 << PC4) |
        (1 << PC3) |
        (1 << PC2) |
        (1 << PC1) |
        (1 << PC0);

    DDRC  &= ~MASK_C;   // INPUT
    PORTC |=  MASK_C;   // PULLUP ON


    // --------------------------------------------------------
    // PORTG
    // PG1, PG0, PG3
    // --------------------------------------------------------
    constexpr uint8_t MASK_G =
        (1 << PG1) |
        (1 << PG0) |
        (1 << PG3);

    DDRG  &= ~MASK_G;   // INPUT
    PORTG |=  MASK_G;   // PULLUP ON


    // --------------------------------------------------------
    // PORTL
    // PL3, PL2, PL1, PL0
    // --------------------------------------------------------
    constexpr uint8_t MASK_L =
        (1 << PL3) |
        (1 << PL2) |
        (1 << PL1) |
        (1 << PL0);

    DDRL  &= ~MASK_L;   // INPUT
    PORTL |=  MASK_L;   // PULLUP ON
}


// ============================================================
// 32個のセンサを読み取る
//
// 戻り値:
//   bit 0～31 に各センサのHIGH/LOWを格納
//
//   HIGH -> 1
//   LOW  -> 0
// ============================================================
uint32_t readSensors()
{
    uint32_t value = 0;


    // --------------------------------------------------------
    // レジスタを先に全部読み取る
    //
    // 同じポートは1回だけ読む
    // --------------------------------------------------------

    const uint8_t b = PINB;
    const uint8_t h = PINH;
    const uint8_t f = PINF;
    const uint8_t a = PINA;
    const uint8_t j = PINJ;
    const uint8_t c = PINC;
    const uint8_t g = PING;
    const uint8_t l = PINL;


    // --------------------------------------------------------
    // PORTB
    // --------------------------------------------------------

    value |= ((b >> PB7) & 1UL) << 0;
    value |= ((b >> PB6) & 1UL) << 1;
    value |= ((b >> PB5) & 1UL) << 2;
    value |= ((b >> PB4) & 1UL) << 3;
    value |= ((b >> PB0) & 1UL) << 4;


    // --------------------------------------------------------
    // PORTH
    // --------------------------------------------------------

    value |= ((h >> PH6) & 1UL) << 5;
    value |= ((h >> PH5) & 1UL) << 6;
    value |= ((h >> PH4) & 1UL) << 7;
    value |= ((h >> PH3) & 1UL) << 8;
    value |= ((h >> PH2) & 1UL) << 9;


    // --------------------------------------------------------
    // PORTF
    // --------------------------------------------------------

    value |= ((f >> PF6) & 1UL) << 10;
    value |= ((f >> PF7) & 1UL) << 11;


    // --------------------------------------------------------
    // PORTA
    // --------------------------------------------------------

    value |= ((a >> PA1) & 1UL) << 12;
    value |= ((a >> PA2) & 1UL) << 13;


    // --------------------------------------------------------
    // PORTJ
    // --------------------------------------------------------

    value |= ((j >> PJ6) & 1UL) << 14;
    value |= ((j >> PJ5) & 1UL) << 15;
    value |= ((j >> PJ4) & 1UL) << 16;
    value |= ((j >> PJ3) & 1UL) << 17;


    // --------------------------------------------------------
    // PORTC
    // --------------------------------------------------------

    value |= ((c >> PC5) & 1UL) << 18;
    value |= ((c >> PC4) & 1UL) << 19;
    value |= ((c >> PC3) & 1UL) << 20;
    value |= ((c >> PC2) & 1UL) << 21;
    value |= ((c >> PC1) & 1UL) << 22;
    value |= ((c >> PC0) & 1UL) << 23;


    // --------------------------------------------------------
    // PORTG
    // --------------------------------------------------------

    value |= ((g >> PG1) & 1UL) << 24;
    value |= ((g >> PG0) & 1UL) << 25;


    // --------------------------------------------------------
    // PORTL
    // --------------------------------------------------------

    value |= ((l >> PL3) & 1UL) << 26;
    value |= ((l >> PL2) & 1UL) << 27;
    value |= ((l >> PL1) & 1UL) << 28;
    value |= ((l >> PL0) & 1UL) << 29;


    // --------------------------------------------------------
    // PG3
    // --------------------------------------------------------

    value |= ((g >> PG3) & 1UL) << 30;


    // --------------------------------------------------------
    // PH7
    // --------------------------------------------------------

    value |= ((h >> PH7) & 1UL) << 31;


    return value;
}


// ============================================================
// setup
// ============================================================
void setup()
{
    Serial.begin(115200);

    initSensors();

    analogWrite(2, 100);
    analogWrite(3, 100);
    analogWrite(4, 100);
    analogWrite(5, 100);
}


// ============================================================
// loop
// ============================================================
void loop()
{
    uint32_t sensors = readSensors();


    // --------------------------------------------------------
    // デバッグ用：32bitのセンサ状態を表示
    // --------------------------------------------------------

    Serial.print("Sensors: ");

    for (int i = 31; i >= 0; --i) {
        Serial.print((sensors >> i) & 1UL);
    }

    Serial.println();

    // --------------------------------------------------------
    // 個別に読み取る例
    // --------------------------------------------------------

    // bit 0 = PB7
    bool sensor0 = (sensors & (1UL << 0)) != 0;

    // bit 1 = PB6
    bool sensor1 = (sensors & (1UL << 1)) != 0;

    // bit 31 = PH7
    bool sensor31 = (sensors & (1UL << 31)) != 0;


    // 例：
    // if (sensor0) {
    //     // PB7がHIGH
    // }


    // --------------------------------------------------------
    // 必要に応じて待機
    // --------------------------------------------------------
    delay(100);
}

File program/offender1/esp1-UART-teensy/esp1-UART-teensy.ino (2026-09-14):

constexpr uint8_t IR_1_PIN = D0;
constexpr uint8_t IR_2_PIN = D1;
constexpr uint8_t IR_3_PIN = D2;
constexpr uint8_t IR_4_PIN = D3;
constexpr uint8_t SDA_PIN = D4;

constexpr uint8_t SCL_PIN = D5;
constexpr uint8_t Switch_1_PIN = D8;
constexpr uint8_t Switch_2_PIN = D10;

void setup() {

  pinMode(Switch_1_PIN, INPUT);
  pinMode(Switch_2_PIN, INPUT);

  Serial.begin(115200);

  // Serial1.setPins(RX, TX);
  Serial1.setPins(D7, D6);
  Serial1.begin(115200);

  Serial.println("Serial1 Started!");
}

void loop() {
  uint8_t send[6];
  send[0] = (1);
  send[1] = (1);
  send[2] = (1);
  send[3] = (1);
  send[4] = (((digitalRead(Switch_1_PIN) << 2) | (digitalRead(Switch_2_PIN) << 1)) & 0b11111110) + 1;
  send[5] = '\0'; // 終端パケット

  for (auto &buf : send) {
    Serial1.write(buf);
    Serial.print(buf);
    Serial.print("\t");
  }
  Serial.print("\n");

  // Serial.print(digitalRead(SW_TOGGLE_1_PIN));
  // Serial.print("\t");
  // Serial.print(digitalRead(SW_TOGGLE_2_PIN));
  // Serial.print("\t");
  // Serial.print(send[4]);
  // Serial.print("\n");

  delay(10);
}

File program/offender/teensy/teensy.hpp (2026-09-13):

#pragma once

#include <cstdint>
#include <array>

namespace robot{
  class Teensy{
   public:
    Teensy() = default;
    ~Teensy() = default;

    void init();
  };
}

namespace robot::pin::teensy{
  static constexpr uint8_t MOTOR_EN = 8;
  static constexpr std::array<uint8_t, 4> MOTOR_PWMs = {9, 10, 11, 12};

  static constexpr uint8_t BALLCATCH_FRONT = 26;
  static constexpr uint8_t BALLCATCH_BACK = 27;

  static constexpr uint8_t KICKER_STROKE = 30;
  static constexpr uint8_t KICKER_CHIP = 31;

  static constexpr uint8_t DRIBBLER_FRONT_EN = 22;
  static constexpr uint8_t DRIBBLER_FRONT_PH = 23;

  static constexpr uint8_t DRIBBLER_BACK = 36;

  static constexpr uint8_t LED = 33;
}

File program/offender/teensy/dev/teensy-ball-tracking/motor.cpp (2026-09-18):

#include "motor.hpp"

Motor motor;

void Motor::init(){
  pinMode(PIN_EN, OUTPUT);
  for(uint8_t i=0; i<NUM; i++){
    analogWriteFrequency(PIN_PH[i], FREQUENCY);
  }
  Serial.println("Motor Initialized");
}

void Motor::output(){
  digitalWrite(PIN_EN, HIGH);
  for(uint8_t i=0; i<NUM; i++){
    motorRaw[i] = motorRaw[i] > 100 ? 100 : motorRaw[i] < -100 ? -100 : motorRaw[i];
    float target = motorRaw[i] * DIR[i];
    uint8_t val = (uint8_t)(127.5f + (target * 127.5f / 100.0f));
    analogWrite(PIN_PH[i], val);
  }
}

// ==================================================

void Motor::calcAvr() {
  static int queueIndex = 0;       // 出力値のキューのインデックス
  static float queueSum[NUM] = {0};  // 各モーターのキュー内の合計値を記録

  for (int i = 0; i < NUM; i++) {
    // キューの合計値から古い値を引き、新しい値を足す
    queueSum[i] -= queue[queueIndex][i];
    queue[queueIndex][i] = motor[i];
    queueSum[i] += motor[i];

    // 平均値を計算
    motorRaw[i] = queueSum[i] / (float)QUEUE_SIZE;
  }

  // インデックスを更新
  queueIndex = (queueIndex + 1) % QUEUE_SIZE;

  return;
}

// ==================================================

void Motor::set(int8_t m0, int8_t m1, int8_t m2, int8_t m3){
  motor[0] = m0;
  motor[1] = m1;
  motor[2] = m2;
  motor[3] = m3;
  return;
}

void Motor::setRaw(int8_t m0, int8_t m1, int8_t m2, int8_t m3){
  motorRaw[0] = m0;
  motorRaw[1] = m1;
  motorRaw[2] = m2;
  motorRaw[3] = m3;
  return;
}

void Motor::setDir(float deg, int8_t power){
  power = power > 100 ? 100 : power < -100 ? -100 : power;

  for(uint8_t i=0; i<NUM; i++){
    uint16_t motorDeg = 90*i + 45;
    motor[i] = (int)(sin((motorDeg - deg) / 180.0f * 3.14159265) * power);
  }
}

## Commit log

2026-05-08 Create メイン基板v1を追加
    回路図シンボルを追加（teensy4.1,ESP32C3など）したり、teensyからラベルを引っ張ったりした
    [main-001-20260509.kicad_pcb, main-001-20260509.kicad_sch]
2026-05-13 Create 電源基板の回路図を進めた
    [power-001-20260513.kicad_pcb, power-001-20260513.kicad_sch]
2026-05-14 Update メイン基板の回路を進めた
    [main-001-20260509.kicad_sch]
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2026-05-14 Create サブ基板の回路図を引き始めた
    [sub-001-20260515.kicad_pcb, sub-001-20260515.kicad_sch]
2026-05-15 Update カメラのRX/TXを修正
    [sub-001-20260515.kicad_sch]
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2026-05-18 Create キッカー基板のDXFファイル(v1)を追加した
    [260518_kikker-substrate_v1.dxf]
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2026-05-19 Create MD基板の回路図を引き始めた
    [md-001-20260519.kicad_pcb, md-001-20260519.kicad_sch]
2026-05-20 Upgrade ファイルの命名法を変えた
    [kikker-substrate_v1_260518.dxf]
2026-05-20 Create 各種基板のDXFファイルをアップした
    [MD-substrate_v1_260520.dxf, Main-substrate_v1_260520.dxf, PowerLine-substrate_v1_260520.dxf]
2026-05-20 Update キッカー基板のv2版をアップした
    [kikker-substrate_v2_260520.dxf]
2026-05-21 Create ラインセンサのDXFファイルをアップした
    [Line-substrate_v1_260521.dxf]
2026-05-24 Update 電源供給基板のDXFファイル
    [PowerLine-substrate_v2_260522.dxf]
2026-05-24 Create ネオピ基板のDXFファイル
    [Neopixel-substrate_v1_260524.dxf]
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2026-05-26 Update メイン基板ほぼアップデートなし
    [main-001-20260509.kicad_sch]
2026-05-28 Update メイン基板はピン関連とレベル変換、サブ基板はESP周りを追加した
    [main-001-20260509.kicad_sch, sub-001-20260515.kicad_sch]
2026-05-28 Update サブ基板完成した
    [sub-001-20260515.kicad_sch]
2026-05-28 Update サブ基板寺田DR後
    [sub-001-20260515.kicad_sch]
2026-05-28 Create ネオピクセル基板完成した
    [main-001-20260509.kicad_sch, neopixel-001-20260528.kicad_pcb, neopixel-001-20260528.kicad_sch]
2026-05-28 Update サブ基板完成
    [sub-001-20260515.kicad_sch]
2026-05-28 Update メイン基板完成した
    [main-001-20260509.kicad_sch]
2026-05-28 Update BSS138周りを修正
    [main-001-20260509.kicad_sch]
2026-05-31 Update メイン基板、キッカー基板、MD基板、供給基板のDXFファイルをバージョンアップした
    [Kikker-substrate_v3_260531.dxf, MD-substrate_v2_260531.dxf, Main-substrate_v2_260531.dxf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]
2026-06-01 Update メイン基板と供給基板のDXFファイルをアップデートした
    [Main-substrate_v3_260601.dxf, PowerLine-substrate_v4_260601.dxf]
2026-06-01 Create 電源基板のDXFファイル（仮）をアップした
    [Power-substrate_v1_260601.dxf]
2026-06-01 Create 精算シート(Excelファイル)を作成した
    [Budget Sheet.xlsx]
2026-06-03 Update MD基板を更新
    [md-001-20260519.kicad_sch]
2026-06-04 Update 収支管理表の内部計算を直した
    [Budget Sheet.xlsx]
2026-06-04 Update MD基板の回路図を完成させた
    [md-001-20260519.kicad_pcb, md-001-20260519.kicad_sch]
2026-06-04 Update MD基板のDXFファイル
    [MD-substrate_v3_260604.dxf]
2026-06-04 Update いろいろ
    [md-001-20260519.kicad_pcb]
2026-06-08 Update ちょっとだけ進めてみたけど...
    [md-001-20260519.kicad_pcb]
2026-06-08 Update ファイルを整理した
    [Shitaita_v1_260522.dxf, body-downside.step, kikkersetcolor.step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]
2026-06-08 Update MD基板、メイン基板、供給基板、電源基板のDXFファイルを更新した
    [Kikker-substrate_v4_260608.dxf, MD-substrate_v4_260608.dxf, Main-substrate_v4_260608.dxf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]
2026-06-09 Create USSの3Dモデルをアップした
    [Cam - USS.f3d]
2026-06-09 Update ネオピク基板、サブ基板、メイン基板のDXFファイルを更新
    [Main-substrate_v5_260609.dxf, Neopixel-substrate_v2_260609.dxf, Sub-substrate_v1_260609.dxf]
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2026-06-09 Update MD基板に触れた
    [md-001-20260519.kicad_pcb]
2026-06-09 Update 場所変更
    [HC-SR04.f3d]
2026-06-11 Update いったんMD完成
    [md-001-20260519.kicad_pcb, md-001-20260519.kicad_sch]
2026-06-11 Update DRしてもらったのでMDを修正更新
    [md-001-20260519.kicad_pcb, md-001-20260519.kicad_sch]
2026-06-12 Update メイン基板の回路図を修正
    [main-001-20260509.kicad_sch]
2026-06-12 Update MD基板、供給基板のDXFファイル
    [MD-substrate_v5_260612.dxf, PowerLine-substrate_v6_260612.dxf]
2026-06-12 Create 後ろ補足センサ基板のDXFファイル
    [BackCatch-substrate_v1_260612.dxf]
2026-06-12 Update メイン基板の回路図をリファクタリングした
    [main-001-20260509.kicad_sch]
2026-06-12 Update 供給基板のDXFファイル
    [PowerLine-substrate_v7_260612.dxf]
2026-06-13 Update メイン基板の回路図仮完成
    [main-001-20260509.kicad_sch]
2026-06-17 Update メイン基板のDXFファイル
    [Main-substrate_v5_260617.dxf]
2026-06-17 Update MD基板のボード図を更新
    [md-001-20260519.kicad_pcb, md-001-20260519.kicad_sch]
2026-06-17 Update メイン基板のボード図に入った
    [main-001-20260509.kicad_pcb, main-001-20260509.kicad_sch]
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2026-06-18 Update メイン基板のDXF
    [Main-substrate_v6_260618.dxf]
2026-06-18 Update メイン基板のPCB完成
    [main-001-20260509.kicad_pcb, main-001-20260509.kicad_sch]
2026-06-18 Update メイン基板をDRした
    [main-001-20260509.kicad_pcb, main-001-20260509.kicad_sch]
2026-06-18 Update キッカー基板の回路図を進めた
    [kicker-001-20260618.kicad_sch]
2026-06-18 Update メイン基板いろいろまとめた
    [main-001-20260509.kicad_sch]
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2026-06-18 Update メイン基板を修正
    [main-001-20260509.kicad_pcb]
2026-06-18 Update メイン基板のREADMEを修正
2026-06-18 Update MD基板のREADMEを修正
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2026-06-19 Update メイン基板のBNO055のGNDに3.3Vが接続されていた問題を解決、ボード図も修正した
    [main-001-20260509.kicad_pcb, main-001-20260509.kicad_sch]
2026-06-19 Update キッカー基板の回路図を完成させた
    [kicker-001-20260618.kicad_pcb, kicker-001-20260618.kicad_sch]
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2026-06-20 Update キッカー基板のDRを受けて修正
    [kicker-001-20260618.kicad_sch]
2026-06-21 Update キッカー基板の回路図をDRに基づいて更新
    [kicker-001-20260618.kicad_pcb, kicker-001-20260618.kicad_sch]
2026-06-21 Update NeoPixel基板の回路図を仮完成させた
    [neopixel-001-20260528.kicad_sch]
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2026-06-21 Update キッカー基板の回路図を修正
    ・電圧計用のコネクタを3ピンに修正
    ・R2を10K→100Kに修正
    [kicker-001-20260618.kicad_sch]
2026-06-21 Update キッカー基板のボード図を更新した
    [kicker-001-20260618.kicad_pcb, kicker-001-20260618.kicad_sch]
2026-06-23 Update 供給基板・ネオピク基板以外のDXFファイルを新しくした
    [Kikker-substrate_260623.dxf, Line-substrate_260623.dxf, MD-substrate_260623.dxf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]
2026-06-24 Update 後ボール補足基板のDXF
    [BackCatch-substrate_260623.dxf]
2026-06-24 Create ボール補足センサの回路図を引いた
    [ballcatch-001-20260624.kicad_pcb, ballcatch-001-20260624.kicad_sch]
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2026-06-24 Update ボール補足センサのフットプリント紐づけ
    [ballcatch-001-20260624.kicad_sch]
2026-06-24 Update キッカー基板のフットプリント紐づけをやった
    [kicker-001-20260618.kicad_sch]
2026-06-24 Create KiCadからメイン基板の3Dモデルを生成
    [.step]
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2026-06-24 Update 供給基板のプロジェクト名を修正
    [relay-001-20260624.kicad_pcb, relay-001-20260624.kicad_sch]
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2026-06-25 Update メイン基板の修正を完了させた
    [main-001-20260509.kicad_pcb, main-001-20260509.kicad_sch]
2026-06-25 Update メイン基板のボード図の修正commitの残り
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2026-06-25 Update サブ基板の回路図を修正した、コネクタを追加できていないので後でやる
    [sub-001-20260515.kicad_sch]
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2026-06-25 Update メイン基板に使用するFPCコネクタを変更・修正
    [main-001-20260509.kicad_pcb, main-001-20260509.kicad_sch]
2026-06-25 Update メイン基板修正のcommit残り
2026-06-25 Update キッカー基板のREADMEを修正
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2026-06-26 Update キッカー基板のQRコードを修正
    [kicker-001-20260618.kicad_pcb]
2026-06-26 Update メイン基板のURLを修正
    [main-001-20260509.kicad_pcb]
2026-06-26 Update MD基板のQRコードのURLを修正した
    [md-001-20260519.kicad_pcb]
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2026-06-26 Update キッカー基板のURLを再度修正した
    [kicker-001-20260618.kicad_pcb]
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2026-06-26 Update キッカー基板の設計者を修正した
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2026-06-27 Update 供給基板を開いてちょっとシルクスクリーンを修正
    [relay-001-20260624.kicad_pcb, relay-001-20260624.kicad_sch]
2026-06-27 Update MD基板のピンソケット→ピンヘッダへの修正を完了させた
    [md-001-20260519.kicad_pcb, md-001-20260519.kicad_sch]
2026-06-27 Update メイン基板のシルクスクリーンを修正した
    [main-001-20260509.kicad_pcb, main-001-20260509.kicad_sch]
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2026-06-27 Update 供給基板のボード図の修正とDR完了、再DR求
    [neopixel-001-20260528.kicad_sch, relay-001-20260624.kicad_pcb, relay-001-20260624.kicad_sch]
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2026-06-28 Update メイン基板のボード図を修正
    [main-001-20260509.kicad_pcb]
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
